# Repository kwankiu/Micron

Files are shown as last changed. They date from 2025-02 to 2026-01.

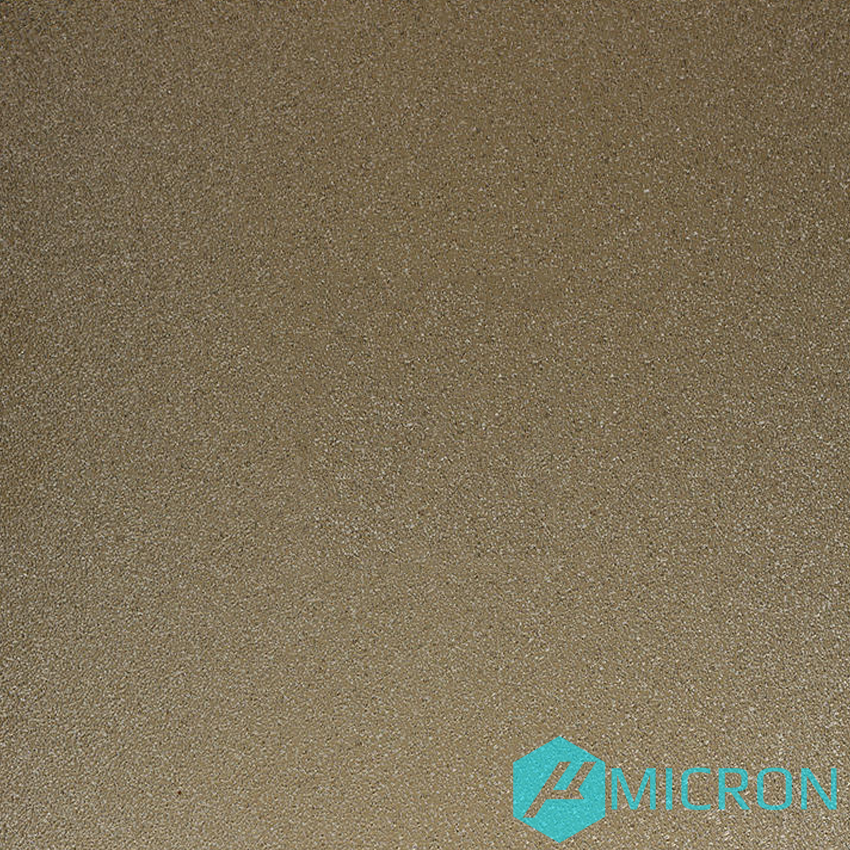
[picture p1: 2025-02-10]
Slicer_Profiles/BedModel/micron_textured.png

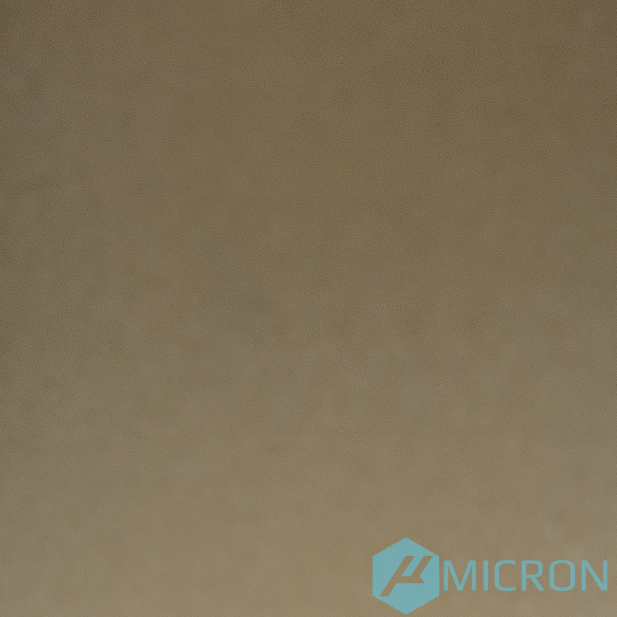
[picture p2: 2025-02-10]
Slicer_Profiles/BedModel/micron_smooth_pei.png

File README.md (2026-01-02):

## Micron M++
Rendering of a Micron build

<p align="center">
  <a aria-label="Stars" href="https://github.com/PrintersForAnts/Micron/stargazers">
    </a> &nbsp;
  <a aria-label="License" href="https://github.com/PrintersForAnts/Micron/blob/master/LICENSE">
    </a> &nbsp;
  <a aria-label="Commits" href="">
    </a> &nbsp;
  <a aria-label="Discord" href="">

</p>

[PFA's Discord](https://discord.gg/doomcube)

[My Micron BOM is here.](https://docs.google.com/spreadsheets/d/1mTU4rc2pGbNT7JGGZr5BcKCps8HXw2-bZYBfcn8UcF8)

### M++ is my own fork of Micron R1 with mods, config and additional STLs

## Changes
- SuperSlicer & OrcaSlicer Profile
- Printer config
- ADXL345 Probe (WIP)
- 230x230 build (WIP)

## Size

<details> 
   <summary>
    120x120 build
    </summary>

## Frame Extrusions
Misumi Part #  |Qty | Notes
 ----|----|----|
HFS3-1515-300 |4 | Blind holes need to be drilled
HFS3-1515-220 |10| Ends need to be tapped (M3)
HFS3-1515-205 |2 |
HFS3-1515-190 |1 |
HFS3-1515-120 |1 |

## Linear Rails
Part  | Qty | Length | Notes
-----|----|----|----|
MGN7H | 6 | 160mm | will work with V0 150mm rails if wanted, but 160mm will work as well and is recommended  
MGN9C OR MGN9H | 1 | 160mm | will work V0 150mm rails but 160 will work as well and is recommended 
</details>

<details>
    <summary>
    180x180 build
    </summary>
    
## Frame Extrusions
Misumi Part #  |Qty | Notes
 ----|----|----|
HFS3-1515-350 |4 | Blind holes need to be drilled
HFS3-1515-280 |10| Ends need to be tapped (M3)
HFS3-1515-265 |2 |
HFS3-1515-250 |1 |
HFS3-1515-180 |1 |

## Linear Rails
Part  | Qty | Length
-----|-----|-----|
MGN7H | 6 | 220mm
MGN9C OR MGN9H | 1 | 220mm 
</details>

<details>
    <summary>
    230x230 build
    </summary>
    
## Frame Extrusions
Misumi Part #  |Qty | Notes
 ----|----|----|
HFS3-1515-400 |4 | Blind holes need to be drilled
HFS3-1515-330 |10| Ends need to be tapped (M3)
HFS3-1515-315 |2 |
HFS3-1515-300 |1 |
HFS3-1515-230 |1 |

## Linear Rails
Part  | Qty | Length
-----|-----|-----|
MGN7H | 6 | 270mm
MGN9C OR MGN9H | 1 | 270mm 
</details>

## No Drop Nuts
There are 2 versions of this mod, 1 from [Zruncho](https://github.com/VoronDesign/VoronUsers/tree/master/printer_mods/zruncho/V0_No_Drop_Nuts) and the other from a user named [Zen3D](https://github.com/VoronDesign/VoronUsers/tree/master/printer_mods/Zen3D/V0_1515_T-nut/). Both of them have their uses. I prefer to use the Zen3D kind just for the fact that the screw can go all the way through the printed part. Zrunchos do have a much nicer fitment into the extrusions but they also dont allow the screw to go all the way through. **NOTE:** the Zruncho nuts will not fit anywhere that has a tab to index to the extrusion - this includes the A/B drives, all idlers, and skirts. If you want to print only one type of nut, use the Zen3d nuts.

## Thank you
Thanks to the following people on Discord who have helped make this printer what it is today. 

- [@KyleGB](https://github.com/Jadecky) - too many additions to name them all
- @TheWarolf#1247
- @L.e.o.p.a.r.d#0990
- @deepfriedheroin#5006
- @JosAr#0517
- @sentein#3903
- @madcat#7838
- @Kyrios#5486
- @faithblinded#1491
- @zruncho#1790
- @Finn#2449
- @clee#1337
- @slidr#4412
- @gfunnymoney#3748
- Jason from LDO
- Voron Dev Team
- all the R1 beta testers
  
[You can support the Micron project on Patreon](https://www.patreon.com/user?u=27661824&fan_landing=true).

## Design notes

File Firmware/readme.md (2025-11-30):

# Micron Firmware Config

run this script in your terminal to download the basic Micron cfg, 

```
cd ~/printer_data/config && curl -s https://api.github.com/repos/PrintersForAnts/Micron/contents/Firmware/printer_data/config | grep download_url | cut -d '"' -f 4 | xargs -n1 curl -sOL
cd ~/printer_data/gcodes && curl -s https://api.github.com/repos/PrintersForAnts/Micron/contents/Firmware/printer_data/gcodes | grep download_url | cut -d '"' -f 4 | xargs -n1 curl -sOL
```

make sure to go through the entire cfg and uncomment the sections required 

* Build Size (120 or 180) 
* MCU
* Toolhead MCU
* Probe

This will download he default config as well as a sample gcode for printing a test cube

to initiate the test cube print, run the macro 

`PRINT_TEST_CUBE` 
then your webui will prompt you to choose which filament type you are using for the test print 


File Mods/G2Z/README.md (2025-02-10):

## Micron Galileo 2 Z-Drive (G2Z)

It is recommened to use the [Z idlers](../R1_Beta/STLs/Z_Idlers/) from the R1 beta folder if using G2Z drives 



The Galileo 2 Z-Drive (G2Z) is designed as a compact Z-drive for the Voron V2 and Micron printers.  It features the same 9:1 planetary gearbox and stepper in an easy-to-assemble package without the need for belts or pulleys (outside of the Z belt and pulley themselves).  This design saves considerable space in the electronics compartment for small V2 printers, as well as the Micron 120 and 180 printers, allowing for more room where it's needed most.

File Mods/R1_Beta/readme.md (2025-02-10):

## Micron R1 Beta 
Rendering of a Micron build
<p align="center">

</p>

<p align="center">
Be sure to check out the Micron R1 beta thread on the Doomcube discord for more information 
</p>

## Change log ##

### 01-20-2025
* fixed issues #143 , #141, #138 , #137
* Updated CAD to RC1 status
* uploaded WIP manual with updated preloaded nut callouts 

### 10-17-2024
* Added G2Z Cad and organized all the STLS (Z drives and skirts) G2Z uses same foot mounts from R1Z and skirt accent pieces 
* fixed Pinned XY joints hole sizes to now all be 3.2mm 
* Updated latest assembly to include [Anthead](https://github.com/PrintersForAnts/AntHead)

### 9-20-2024
* increased tension travel on the front idlers by 5mm (from 3mm to 8mm) , minor changes to the front cover of the idler as well

### 9-18-2024
* fixed incorrect counterbore bridging on the rear bowden entry files (thanks to user named Yell for finding that)

### 9-12-2024
* added CNC gantry top bearing mount
* Updated all the umbilical mounts to accomodate the new top bearing mount, as it was interfearing
* removed the YC8 version of the umbilical
* updated cad assembly to v59 

### 9-10-2024
* Added new top bearing support for a double shear bearing on the AB motors 

### 9-5-2024
* cleaned up main cad assembly 
* posted link to fusion source assembly file to be downloaded
* adjusted gantry files to no longer need built in printed shim, now there are shims on both sides of every bearing stack 

### 9-3-2024
* added missing filter files 
* fixed naming issues on certain files 

### 9-2-2024
* added new under bed carbon filter
* started on CAD assembly clean up 
* renamed various files 

### 8-22-2024 
* cleaned up files

### 8-11-2024
* updated the Hula foot mounts to the latest version that works with the bottom panel
* added new TFT35 display front skirt 
* updated latest cad assembly v55
* removed old cad files no longer needed (moved hula cad files into main assembly)

### 8-2-2024
* organized panel clip files
* updated latest cad assembly v54
* added dual color rear bowden entry option

### 8-1-2024
* Updated Z drives for better printability to match new skirt accent pieces
* Added under bed filter from KyleGB to the main repo (still need STLs)

### 7-27-2024
* fixed waveshare accent pieces
* updated latest cad assembly v52
* updated skirts with new accent pieces as well as bottom panel mounting provisions

### 7-25-2024
* Updated z belt cover accent cover to fit better
* added twist lock panel clips for 3mm foam and panels
* fixed printing orientation for rail stops and umbilical mounts

### 7-23-2024
* Updated R1 Skirts to now include accent strips along the bottom as well as allow for a bottom panel to fit
* Updated skirts to they are all the same height , some had about ~1mm difference between them 
* Updated the waveshare mount to now us m2 self tapping screws instead of filament to keep bezel on 
* Updated Z drive foot mount to accommodate  bottom panel 

### 7-23-2024
* Update Beacon mount to work with older Rev D beacon probes 
* Added a new rear bowden entry set, supporting m10 collet, ECAS collet, or No collet 
* Added R1 style stock panel clips (tool less panel clips are coming soon as an option as well)
* Added fixed Z belt covers to better fit with the R1 Z belt location
* Organized the panel file directory 

### 7-15-2024
* Added Beacon probe mount

### 7-08-24
* Added 120x120 build R1 Cad assembly
* Added rear skirts for 120x120 builds 
* Organized files into 120 and 180 specific folders 

### 7-05-24
* added rear power inlet skirts
* updated printed rail stops to match the style of R1 update (low poly look)
* added keystone blank model to fill the keystone slots on the rear skirt if not used 

### 7-02-24
* updated Z drive tensioner body to use longer m3x25 instead of m3x20
* added optional Hula feet adapters for R1 and G2Z
* updated latest cad assembly

### 6-18-24
* uploaded side skirts and 4.3 waveshare display front skirt

### 6-2-24
* changed hex pattern on Z drives to make them easier to print 

### 5-21-24
* adjust the location of the Z gantry belts pulley to fit in the front idlers better ([#124](https://github.com/PrintersForAnts/Micron/issues/124))

### 5-14-24
* fixed z drive issue with inconsistencies with both A and B z drives ([#120](https://github.com/PrintersForAnts/Micron/issues/120))
* updated z tensioner bearing overhang to be easier to print ([#122](https://github.com/PrintersForAnts/Micron/issues/122))

### 5-7-24
* Added ziptie spot on to klicky dock

### 5-6-24
 * Updated Z drives to fit powge and formbot metal 64T pulleys ([#115](https://github.com/PrintersForAnts/Micron/issues/115))
 * Updated Z idlers to fit toothed pulleys with a flange of 13mm OD ([#116](https://github.com/PrintersForAnts/Micron/issues/116))
 * raised klicky dock , it was hanging too low ([#117](https://github.com/PrintersForAnts/Micron/issues/117))
 * updated spool holder to now work with 3mm foam ([#118](https://github.com/PrintersForAnts/Micron/issues/118))

### 4-6-24
 * added pushed rigid z joints
 * new z belt covers
 * new bowden tube holder
 * new removable spool holder (modified from LDOs)

### 4-5-24
  *  Added Nema14 Z motor mounts

### 4-3-24
  * New beta rev2 Z drives with the 152mm belt loops
  * Shrunk entire body by 5mm or so
  * rotated the Z drives 180deg, this makes it easier to retention the closed loop belts after they are assembled if needed (thanks [@Squirrel-brain](https://github.com/Squirrel-brain)) 

### Initial Beta Release
Gantry 
  * Swapped rear extrusion and Z chain around
  * Fixed all belt path issues with the gantry
  * Gave every piece a low poly / stealthy look to them
  * New z joints that are stronger/ less prone to cracking
  * Added support for 3mm pins OR screws for the gantry
  * Removed support for the printed Z chain (will revisit later)
  * Implemented the BFI idlers for the AB belts
  * Modified the BFI idlers from clees repo to fix the belt path for the R1 gantry 
    
Z axis
  * New Z drives that use 152mm belt loops with proper belt tensioning 
  * Implemented the BZI idlers for the Z belts
  * Modified BZI to support both toothed idlers and bearing stacks (there are different parts named accordingly)

Panels/Door/Skirts
  * New door hinge/ latch system that no longer needs the magnet latch on the inside of the printer
  * Door now needs 3mm foam to help seal the enclosure better
  * Panel clips will be coming later as will skirts

## BOM Changes (Subject to change)
Item  |Qty | Notes
 ----|----|----|
GT2-16-Toothed Idler | 6 | XY-Joints and Z idlers now use toothed idlers by default, bearing stacks will still work 
GT2-152mm closed loop belt | 4 | New Z drives use 152mm belt loops instead of the 188mm 
screws | IDK | i havent gone through and checked the changes for the hardware as of yet 
MGN9H | 1 | X rail is now going to be spec as an MGN9H rail instead of MGN9C to support boop natively 
Klicky_PCB | 1 | now offical support optional as standard klikcy is still supported 
BIQU_microprobe | 1 | also now an official supported mount for those that want to use it

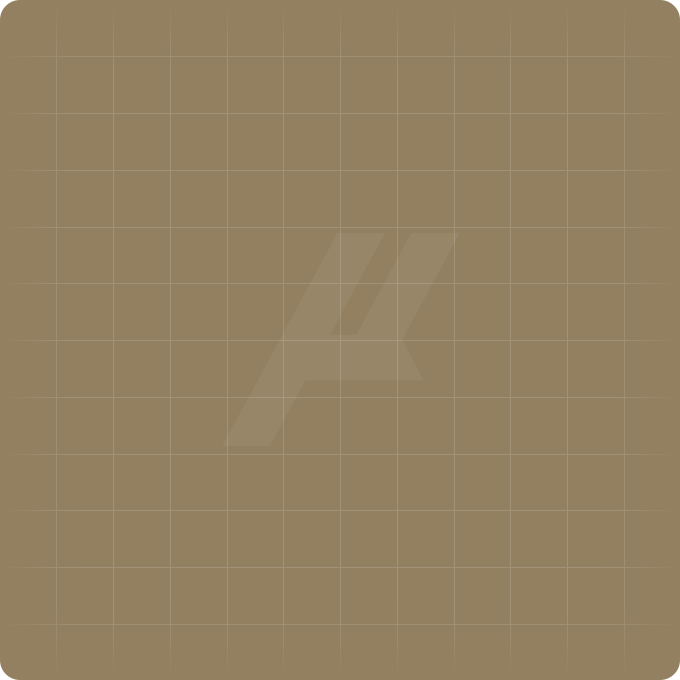
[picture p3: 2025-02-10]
Slicer_Profiles/BedModel/micron-120-grid.png

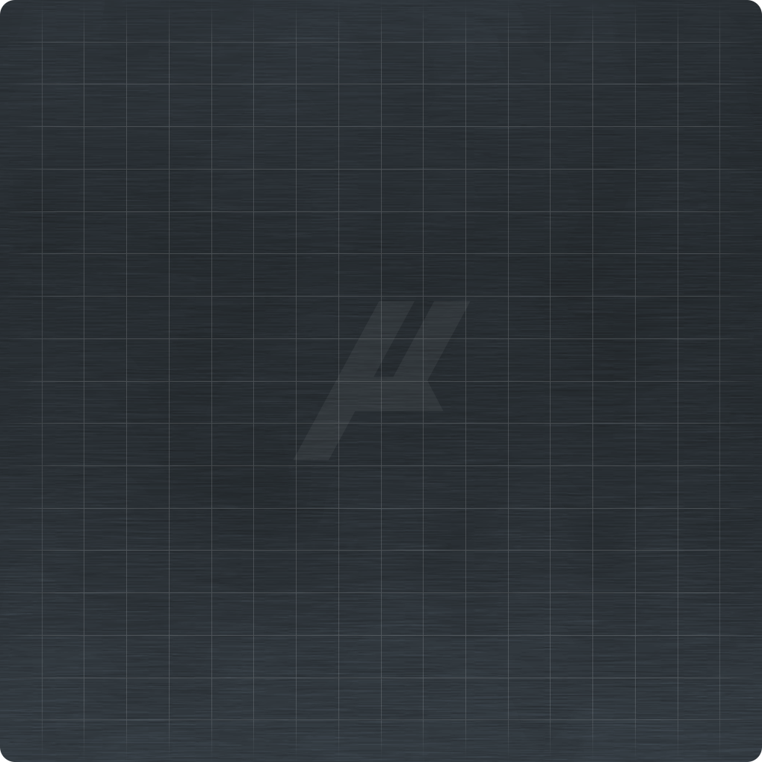
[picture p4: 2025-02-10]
Slicer_Profiles/BedModel/micron-180-grid-blue.png

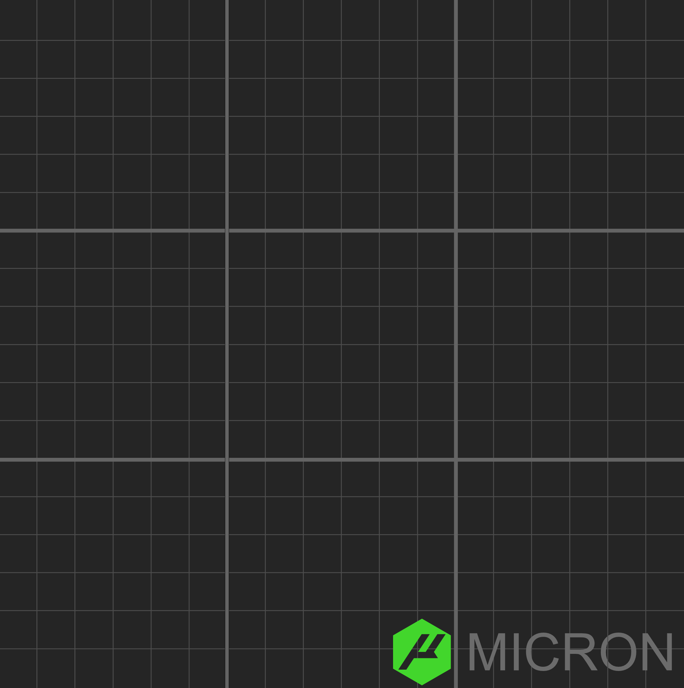
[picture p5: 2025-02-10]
Slicer_Profiles/BedModel/micron-180-grid-green.png

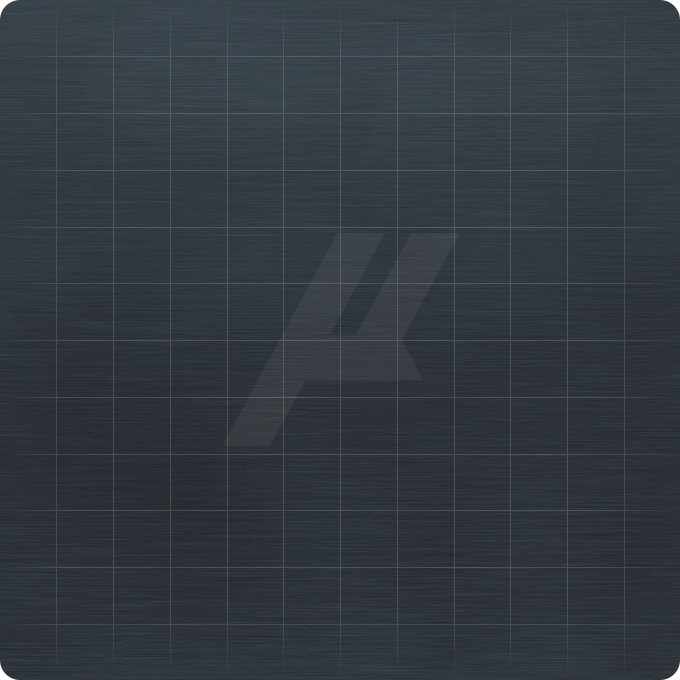
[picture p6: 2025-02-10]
Slicer_Profiles/BedModel/micron-120-grid-blue.png

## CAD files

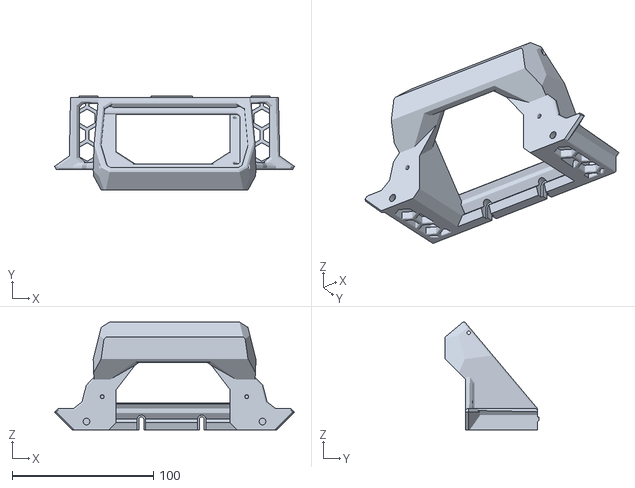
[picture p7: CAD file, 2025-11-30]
STLs/Skirts/Displays/TFT35/main_housing.stl
169.9 x 66.6 x 76.4

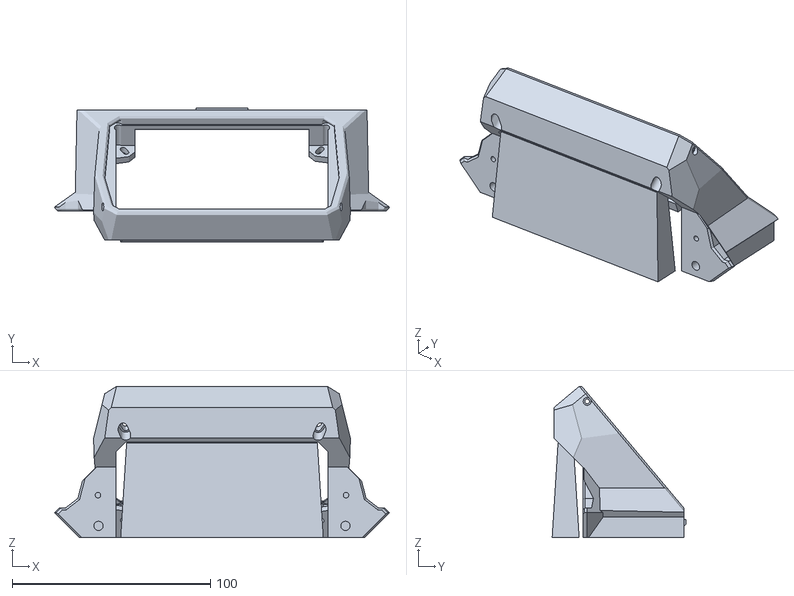
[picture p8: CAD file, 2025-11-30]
STLs/Skirts/Displays/Waveshare43_BTT43/waveshare_btt43_main_housing_x1.stl
169.0 x 67.5 x 76.4

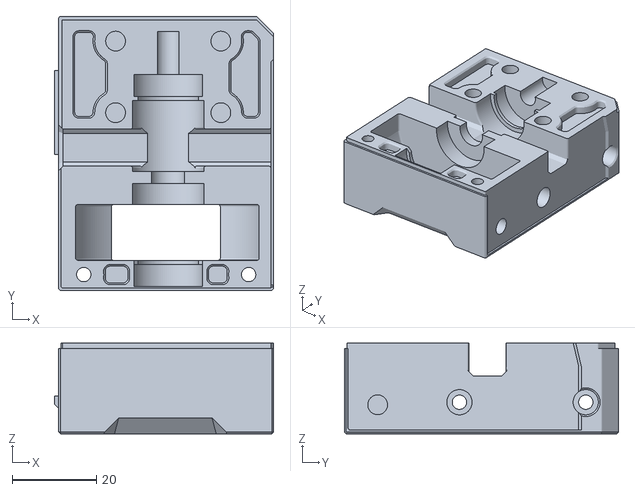
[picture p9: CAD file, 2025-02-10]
STLs/Z_Drive/main_body_a_x2.stl
52.0 x 65.1 x 21.5

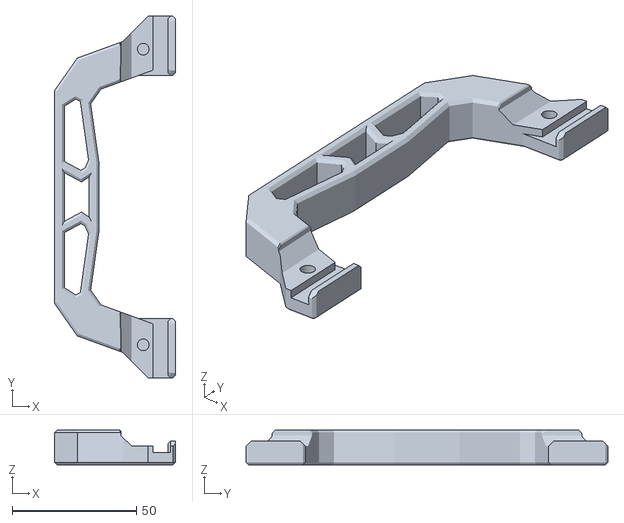
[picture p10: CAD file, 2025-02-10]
STLs/MISC/main_handle_x2.stl
48.8 x 145.7 x 14.1

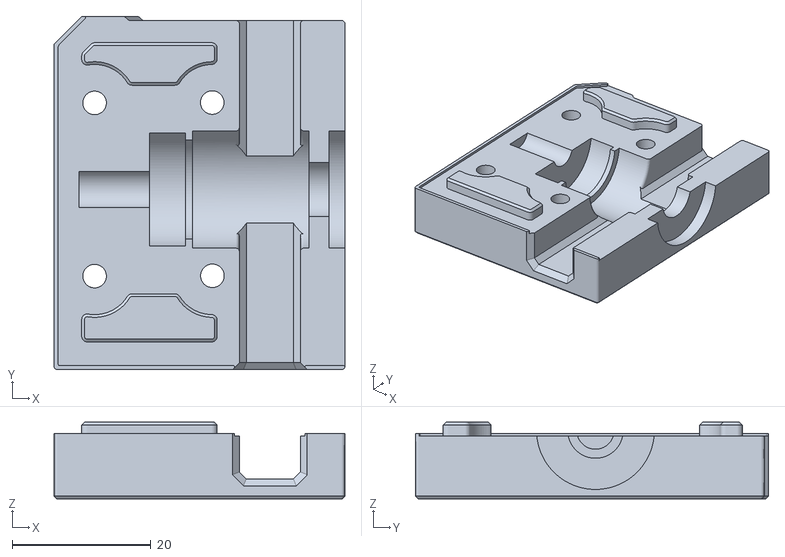
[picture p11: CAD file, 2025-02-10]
STLs/Z_Drive/[a]_shaft_assembly_cover_b_x2.stl
42.0 x 51.0 x 11.0

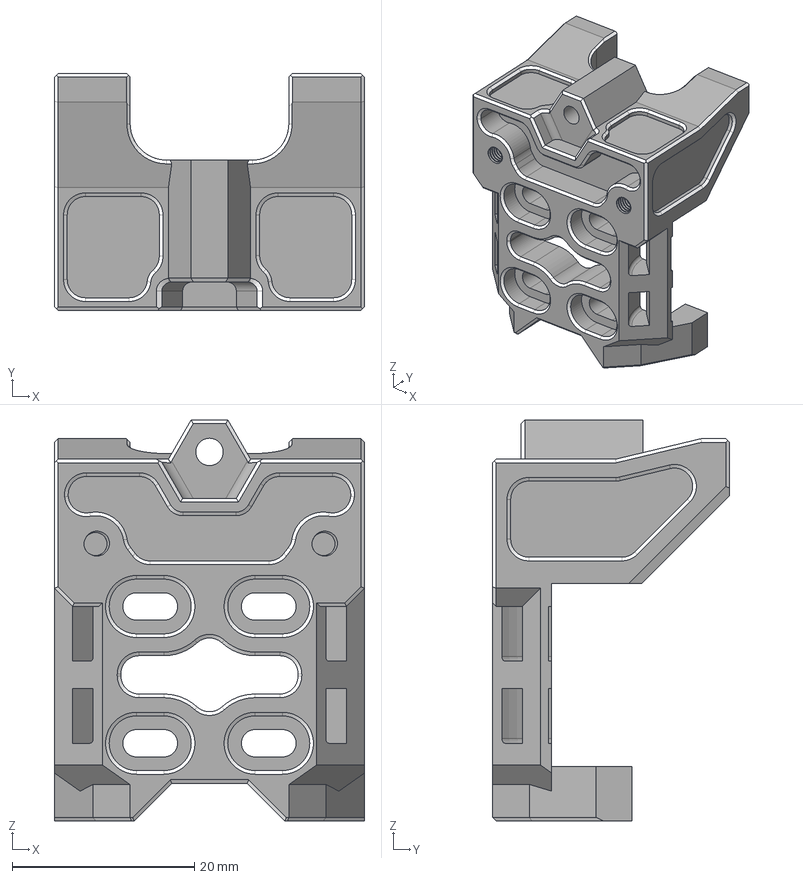
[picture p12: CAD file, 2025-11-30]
CAD/SubAssemblies/CNC_Carriage.step
34.0 x 26.0 x 44.0 mm
MiniSB X Carriage
MGN9H v1 v1
MiniSB X Carriage (2)
M3x6 SCHS (1)
M3x6 SCHS (1) (1)

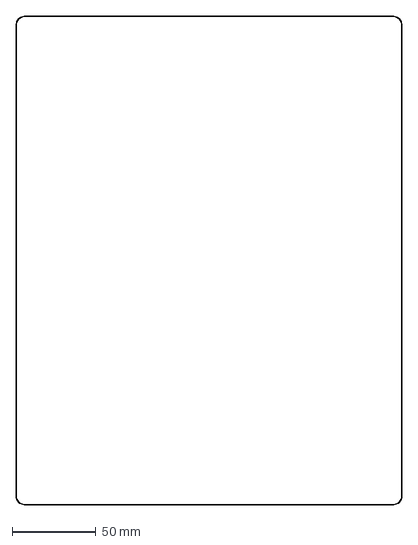
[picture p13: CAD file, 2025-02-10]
Drawing_DXFs/120/door_panel_x1.dxf
230.0 x 291.0 mm

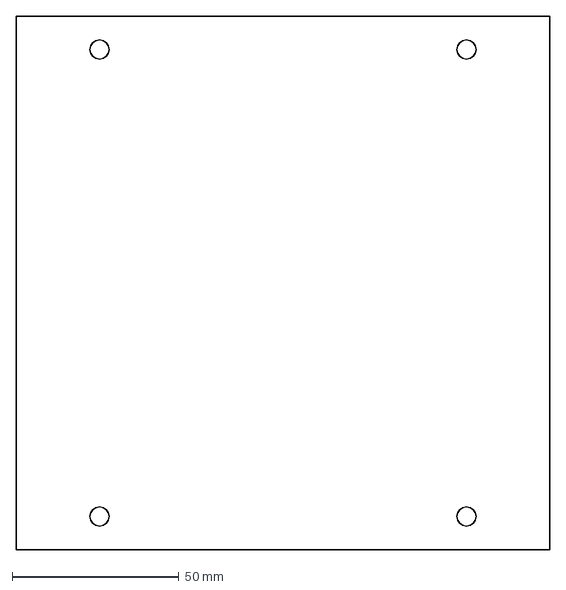
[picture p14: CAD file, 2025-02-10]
Drawing_DXFs/180/Micron-160-Bed.dxf
160.0 x 160.0 mm

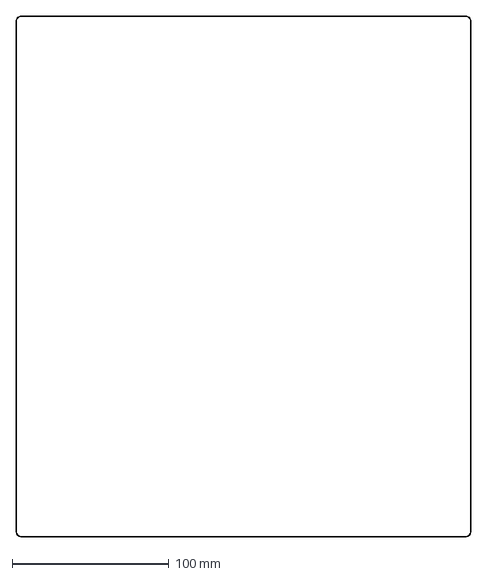
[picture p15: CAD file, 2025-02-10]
DXFs/TRANSPARENT_Side_and_DoorPanel_x3.dxf
290.0 x 332.0 mm

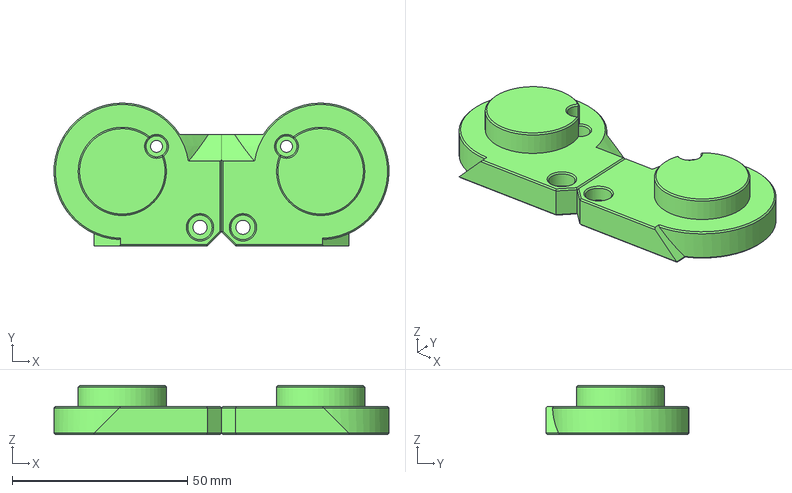
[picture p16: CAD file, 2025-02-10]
Mods/G2Z/CAD/Micron_Hula_G2Z_Feet.step
95.6 x 40.8 x 14.0 mm
Micron_Hula_G2_Z_Drive_Base_Plate_A
Micron_Hula_G2_Z_Drive_Base_Plate_B

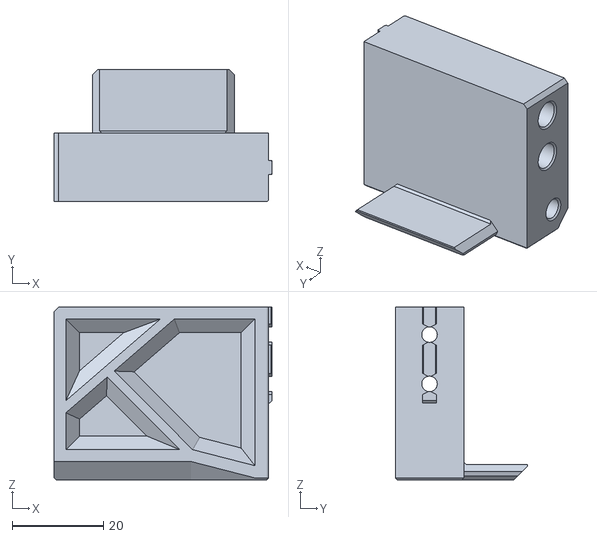
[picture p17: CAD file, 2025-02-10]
Mods/G2Z/STLs/Z_Drives/g2_z_skirt_corner_b_x2.stl
47.7 x 29.0 x 37.8

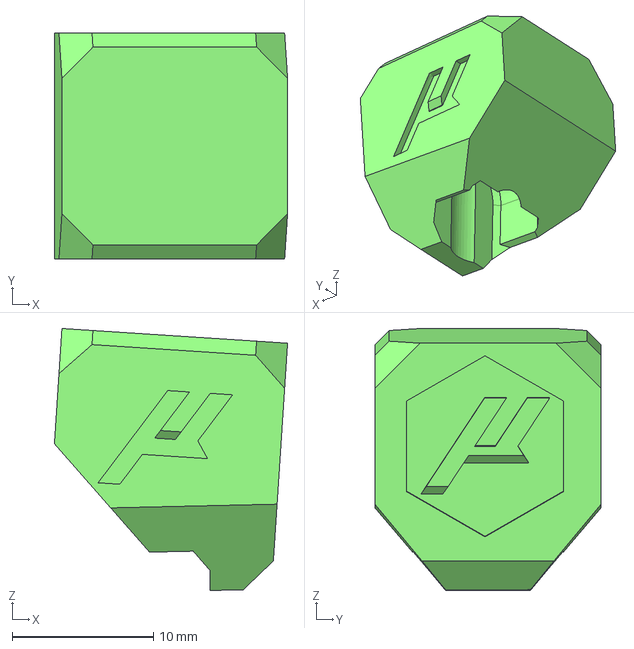
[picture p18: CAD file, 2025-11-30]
Mods/hartk1213/Dummy13_Parts/Micron_Cube_head.step
16.5 x 16.0 x 18.5 mm

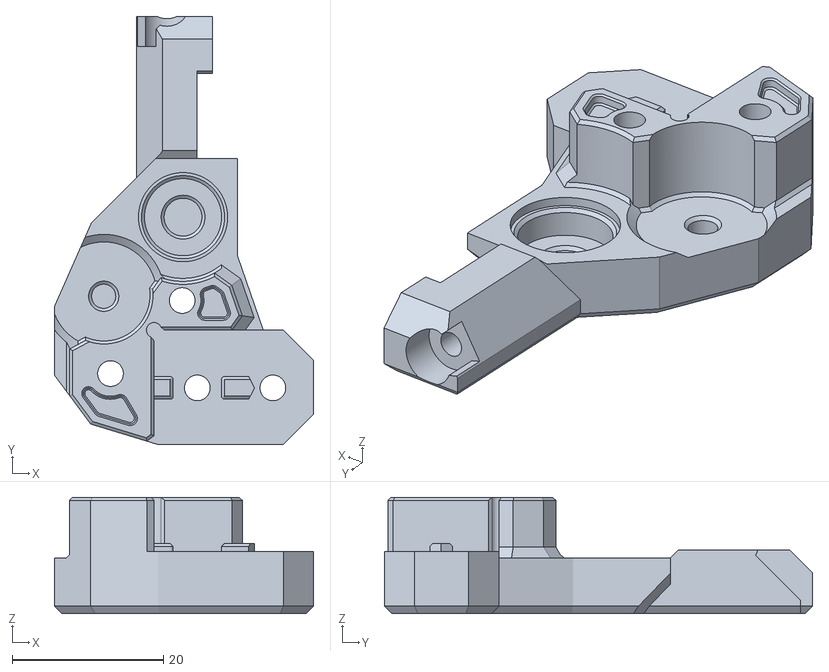
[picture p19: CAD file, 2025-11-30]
Mods/hartk1213/LiveIdler_XY_Joints_LeafCutter/xy_joint_upper_left_live_idlers_LC_x1.stl
34.3 x 56.7 x 15.4

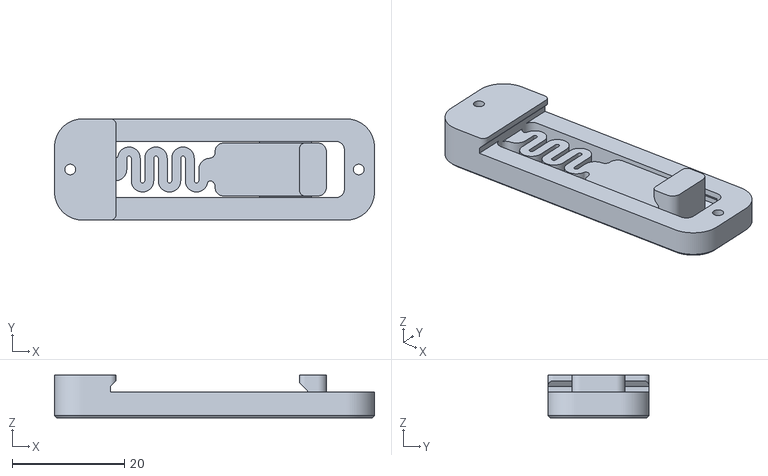
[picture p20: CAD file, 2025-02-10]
Mods/R1_Beta/STLs/Electronics/pcb_din_clip_x3.stl
56.9 x 18.0 x 7.60

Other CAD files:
STLs/Z_Drive/[a]_shaft_assembly_cover_a_x2.stl
STLs/Z_Drive/main_body_b_x2.stl
Mods/R1_Beta/STLs/MISC/Filter/[a]_cartridge_removal_key.stl
Mods/R1_Beta/STLs/Panels/corner_clip_x16.stl
CAD/SubAssemblies/1515_ParametricPanelClips.f3z
DXFs/180_bottom_panel.dxf
DXFs/BLACK_DeckPanel_x1.dxf
DXFs/BLACK_RearPanel_x1.dxf
DXFs/Micron+_MIC6_Bed.step
DXFs/Micron-PrusaMini-Mic6-Bed.dxf
DXFs/TRANSPARENT_TopPanel_x1.dxf
Drawing_DXFs/120/back_panel_x1.dxf
Drawing_DXFs/120/bottom_panel_x1.dxf
Drawing_DXFs/120/deck_panel_x1.dxf
Drawing_DXFs/120/micron_backers.dxf
Drawing_DXFs/120/side_panel_x2.dxf
Drawing_DXFs/120/top_panel_x1.dxf
Drawing_DXFs/180/BottomPanel.dxf
Drawing_DXFs/180/Micron_PrusaMini_MIC6_Bed.step
Mods/G2Z/STLs/Skirts/side_skirt_a_x2.stl
Mods/G2Z/STLs/Skirts/side_skirt_b_x2.stl
Mods/G2Z/STLs/Z_Drives/[a]_g2_z_drive_base_plate_a_x2.stl
Mods/G2Z/STLs/Z_Drives/[a]_g2_z_drive_base_plate_b_x2.stl
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

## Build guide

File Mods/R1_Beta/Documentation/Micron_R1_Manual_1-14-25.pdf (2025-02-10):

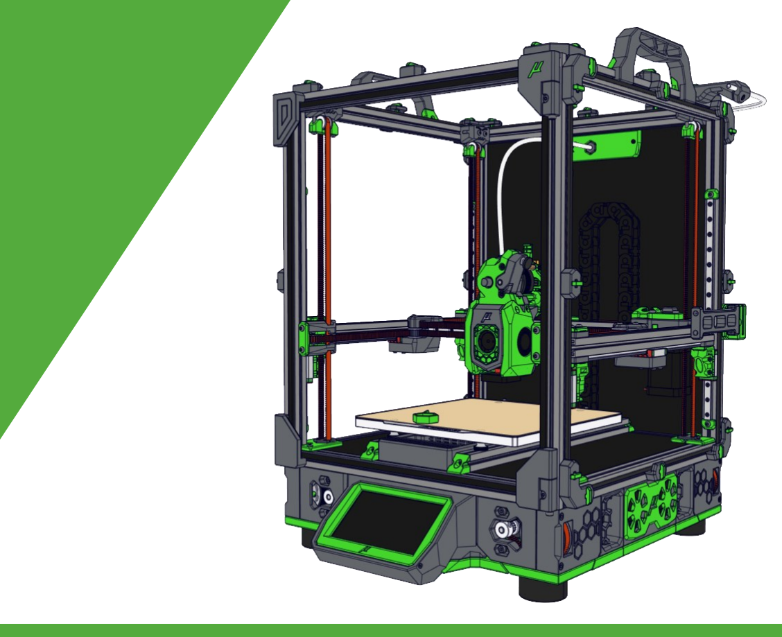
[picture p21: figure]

## VERSION 01/14/2025

# ASSEMBLY MANUAL

Everything is smaller but the price.

M

R1

# icron

TABLE OF CONTENTS

INTRODUCTION | MICRON

## STL FILE KEY

## PRINT GUIDELINES

The STL naming convention used for Micron is the same as that used for VORON printers:

The recommended print settings are also those used for VORON printers:

### PRIMARY COLOR

Example
z_drive_main_a_x2.stl
These files will have nothing at the start of the filename.

### ACCENT COLOR

Example
[a]_z_drive_baseplate_a_x2.stl These files will have ‘’[a]’’ to the front to mention that they are intended to be printed with an accent color.

### QUANTITY REQUIRED

Example
[a]_z_drive_baseplate_a_x2.stl If a file ends with ‘’_x#’’, that is telling you the quantity of that part required to build this system..

FDM MATERIAL
Micron was designed for ABS. Use other plastics at your own discretion.
LAYER HEIGHT
Recommended : 0.2mm
EXTRUSION WIDTH
Recommended : Forced 0.4mm INFILL PERCENTAGE
Recommended : 40%

INFILL TYPE
Grid, Gyroid, Honeycomb, Triangle, Cubic, Adaptive Cubic.
WALL COUNT
Recommended : 4
SOLID TOP/BOTTOM LAYERS
Recommended : 5
SUPPORTS REQUIRED
If the part needs supports, they are built into the model.
INTRODUCTION | MICRON

HOW TO GET HELP

If you need assistance with your build you can head over the DOOMCUBE Discord server and post your questions ( typically in the #micron_build_questions channel ). It is the primary help channel for the Micron! You can also check the Github page for the latest releases.

DISCO? OH …DISCORD
If you need assistance with your build you can head over the DOOMCUBE Discord server and post your questions ( typically in the #micron_build_questions channel ). It is the primary help channel for the Micron!

GIT GUD
If you want to stay up to date on the latest files for Micron. The github page is the only source for the latest files.
HARDWARE - REFERENCES | MICRON

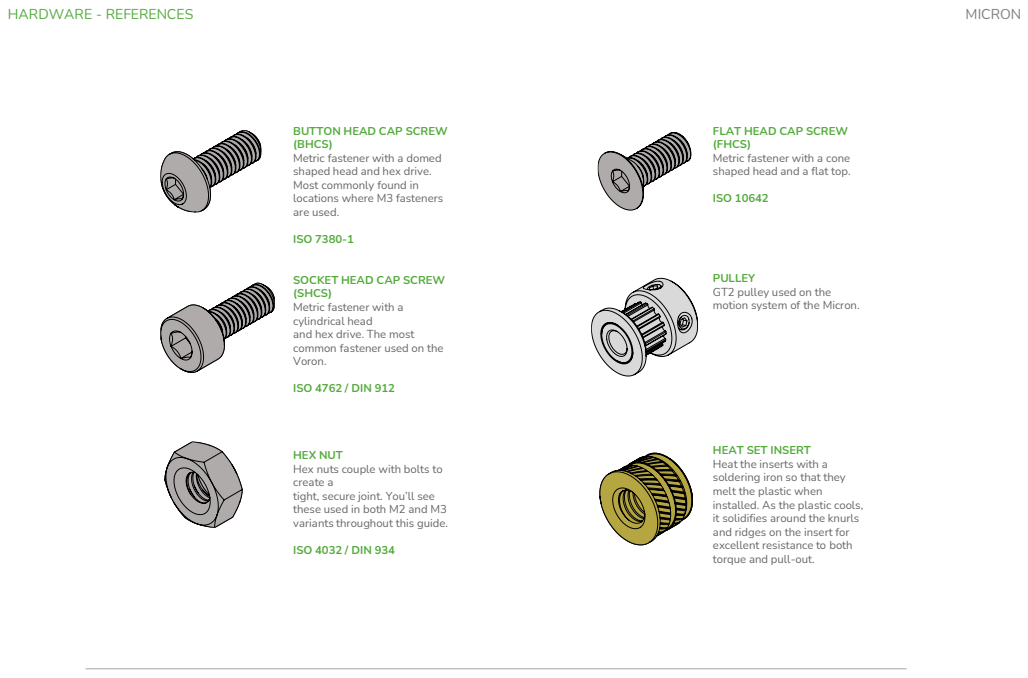
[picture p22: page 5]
HARDWARE - REFERENCES; MICRON

BUTTON HEAD CAP SCREW
(BHCS)
Metric fastener with a domed
shaped head and hex drive.
Most commonly found in
locations where M3 fasteners
are used.
ISO 7380-1

FLAT HEAD CAP SCREW
(FHCS)
Metric fastener with a cone
shaped head and a flat top.
ISO 10642

SOCKET HEAD CAP SCREW
(SHCS)
Metric fastener with a
cylindrical head
and hex drive. The most
common fastener used on the
Voron.
ISO 4762 / DIN 912

PULLEY
GT2 pulley used on the
motion system of the Micron.

HEAT SET INSERT
Heat the inserts with a
soldering iron so that they
melt the plastic when
installed. As the plastic cools,
it solidifies around the knurls
and ridges on the insert for
excellent resistance to both
torque and pull-out.

HEX NUT
Hex nuts couple with bolts to
create a
tight, secure joint. You’ll see
these used in both M2 and M3
variants throughout this guide.
ISO 4032 / DIN 934

SELF TAPPING SCREW
Fastener with a pronounced
thread profile that is screwed
directly into plastic.

F623 BEARING
A ball bearing with a flange
used in various gantry
locations.

M3 SHIMS
Not to be confused with
stamped washers. These are
used in all M3 call-out
locations in this manual.
3x6x0.5 DIN 988

625 BEARING
A ball bearing with used in
the Z drive.

5mm x 47mm Shaft
Steel shaft, 5mm in diameter,
47mm long with a flat ground
on it used in the Z drive gear
box assembly

GRUB SCREW (GS)
Metric Socket Cup Point Set
Screws (also called Hollow
Point Grub Screws) are fitted
with a concave cup point,
which allows them to fit
closely against a rounded
surface such as a motor shaft.
ISO 4029/ DIN 916

MICRON Logo
Look for Micron Logo next to the printed part, this is a direct link to the file on the github repo.

ATTENTION BUBBLE
This logo denotes steps that are common areas that
mistakes can occur.

HARDWARE - REFERENCES

M3x8 SHCS

Look for the GREEN call
outs to mention the
various hardware used
(5) Bottom – 180

Look for the BLACK call outs to mention the preloaded M3 nuts, NOTE: some of them are specific to the size of printer and will be in bold at the end

MICRON

(3) outside

Look for the GRAY call outs to mention the preloaded M3 nuts that are optional, Some of the printed parts have a printed twist lock version to attach to the frame OR a screwed-on version. If you choose to use the twist lock then you can ignore the gray nut call outs

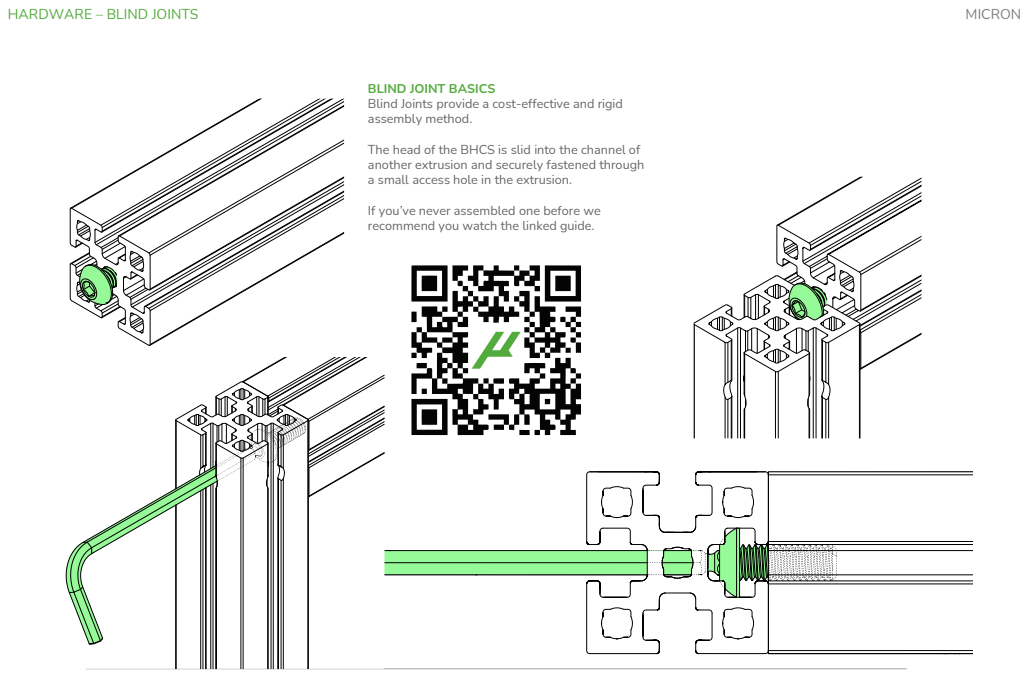
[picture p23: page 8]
HARDWARE – BLIND JOINTS; MICRON

BLIND JOINT BASICS
Blind Joints provide a cost-effective and rigid
assembly method.
The head of the BHCS is slid into the channel of
another extrusion and securely fastened through
a small access hole in the extrusion.
If you’ve never assembled one before we
recommend you watch the linked guide.

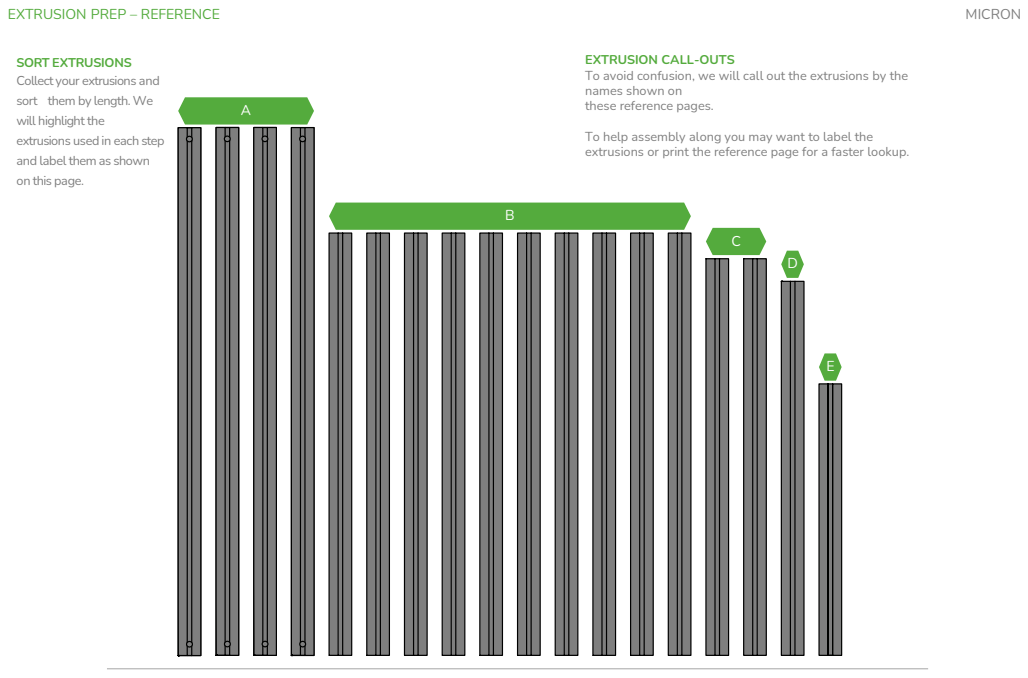
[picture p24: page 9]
EXTRUSION PREP – REFERENCE; MICRON

SORT EXTRUSIONS
Collect your extrusions and
sort them by length.We
will highlight the
extrusions used in each step
and label them as shown
on this page.

EXTRUSION CALL-OUTS
To avoid confusion, we will call out the extrusions by the
names shown on
these reference pages.
To help assembly along you may want to label the
extrusions or print the reference page for a faster lookup.

BED EXTRUSIONS?
Some frame kits come with bed
extrusions that are mounted using
blind joints. These will end up being 2
longer extrusions and 8 B extrusions.

MULTIPLE VIEWS
The views shown are the left, front, right, and
bottom views of each extrusion.

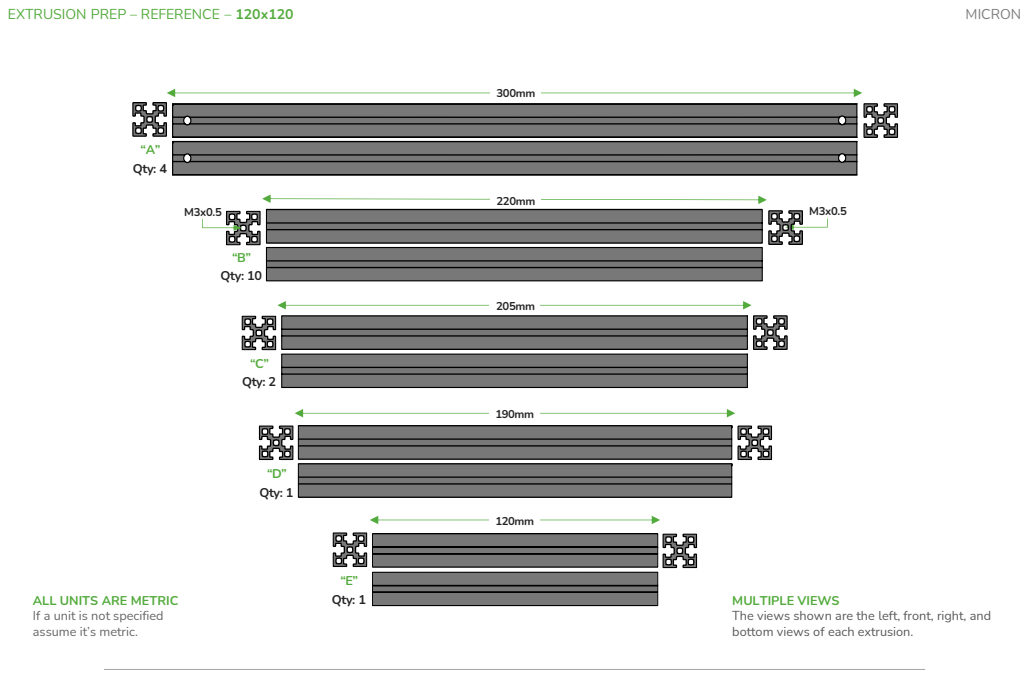
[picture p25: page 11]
“A” Qty: 4; “B” Qty: 10; “C” Qty: 2; “D” Qty: 1; “E” Qty: 1; MICRON

EXTRUSION PREP – REFERENCE – 120x120

ALL UNITS ARE METRIC
If a unit is not specified
assume it’s metric.

MULTIPLE VIEWS
The views shown are the left, front, right, and
bottom views of each extrusion.

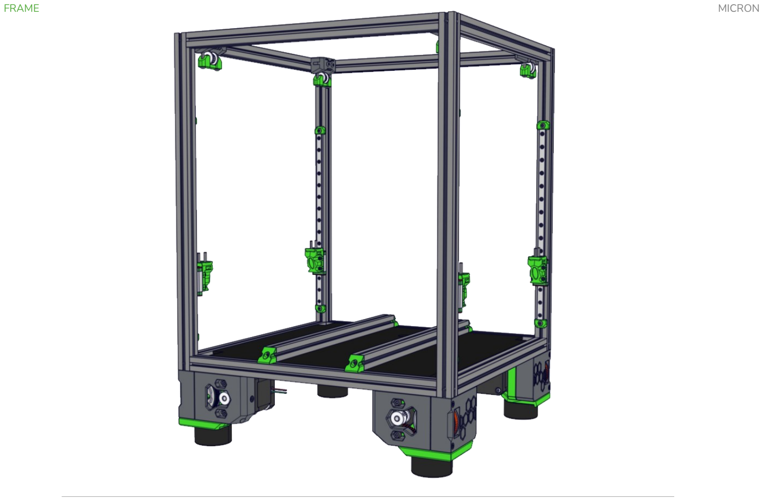
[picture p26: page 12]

FRAME | MICRON

PREPARE 8 EXTRUSIONS
These extrusions are going to be used in
this section. Prepare them as shown above
by partially threading in an M3x8 BHCS
in either side.

POPULATING NUT CARRIERS
Pictured shows all the m2 nuts populated, but depending on how much M2 hardware you sourced, you may not be able to fully populate the M2 Nut Adapters if that happens, skipping

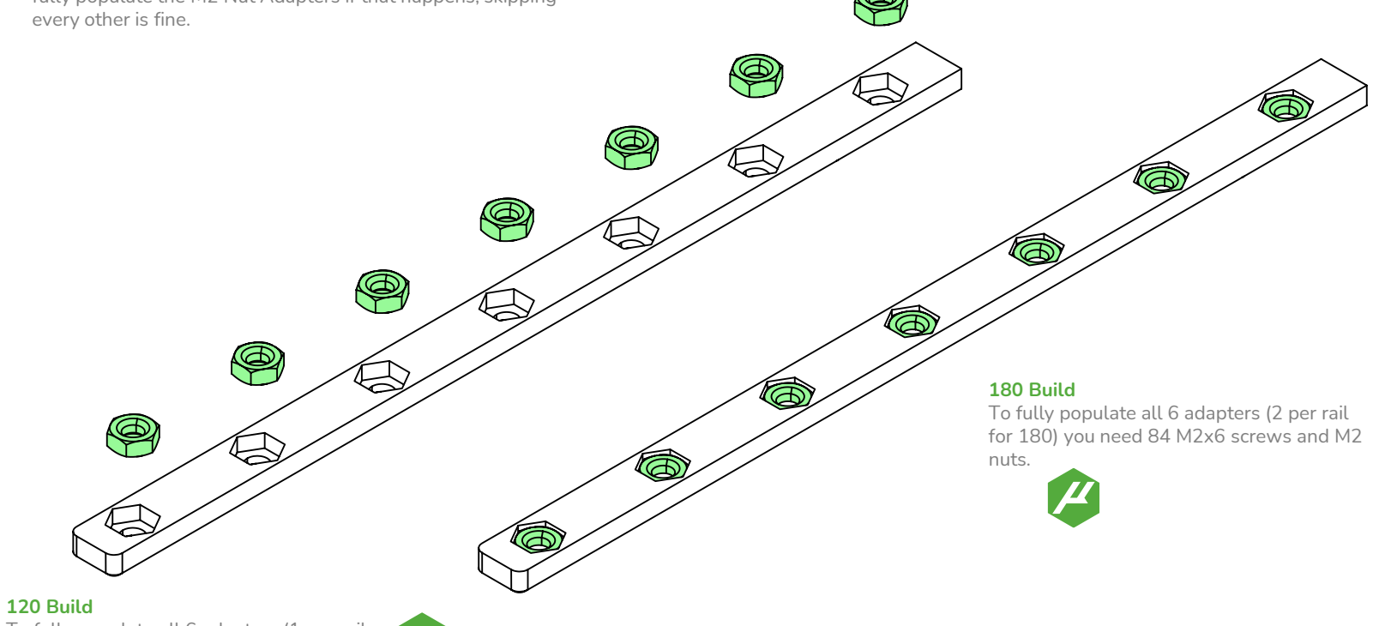
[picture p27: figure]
every other is fine.; 180 Build; for 180) you need 84 M2x6 screws and M2 nuts.; 120 Build

To fully populate all 6 adapters (2 per rail

To fully populate all 6 adapters (1 per rail for 120) you need 60 M2x6 screws and M2 nuts.

FRAME – Z RAILS | MICRON

M2x6 SHCS

M2 Hex Nut

Z RAILS ALIGNMENT

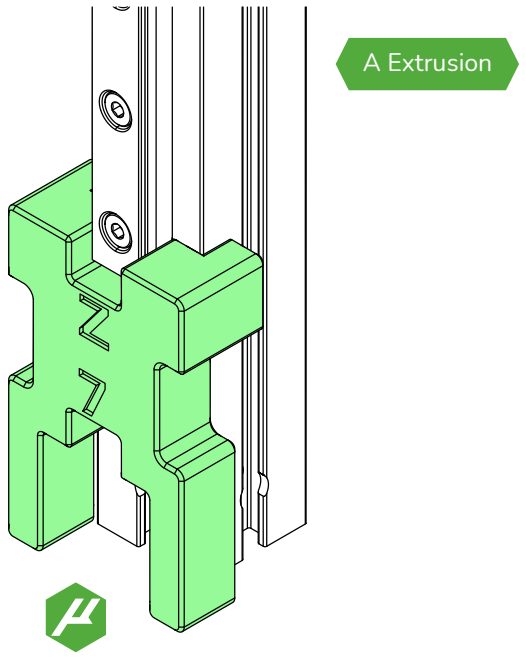
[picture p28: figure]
A Extrusion

Z rails are mounted before assembly of the frame. Stand up one of the A extrusions and use the printed rail alignment tool as shown to align the bottom of the rail. The rail end should be 36mm from the bottom of the extrusion. Use a second rail alignment tool on the upper half of the rail, using the section marked ‘7’, to properly center the rail on the extrusion. Tighten the screws, being careful to maintain the alignment provided by the printed tools. Repeat this process for all 4 A extrusions and their rails.

FRAME – Z RAILS | MICRON

RAIL STOPS
With the Z rails installed, the rail stops can now be added to both ends. Loosely screw an M3x8 BHCS. Repeat for both ends of all 4 Z rails. Now you can work on the build without risking a Z carriage flying off its rail.

WHERE’S THE NUT!?
The instructions won’t call out nuts that were inserted in a previous step, nor nuts that can be easily inserted in the current step. if a screw does NOT thread into a nut we will explicitly state this. You can assume that all screws that enter extrusion slots thread into a nut.
FRAME – Z RAILS | MICRON

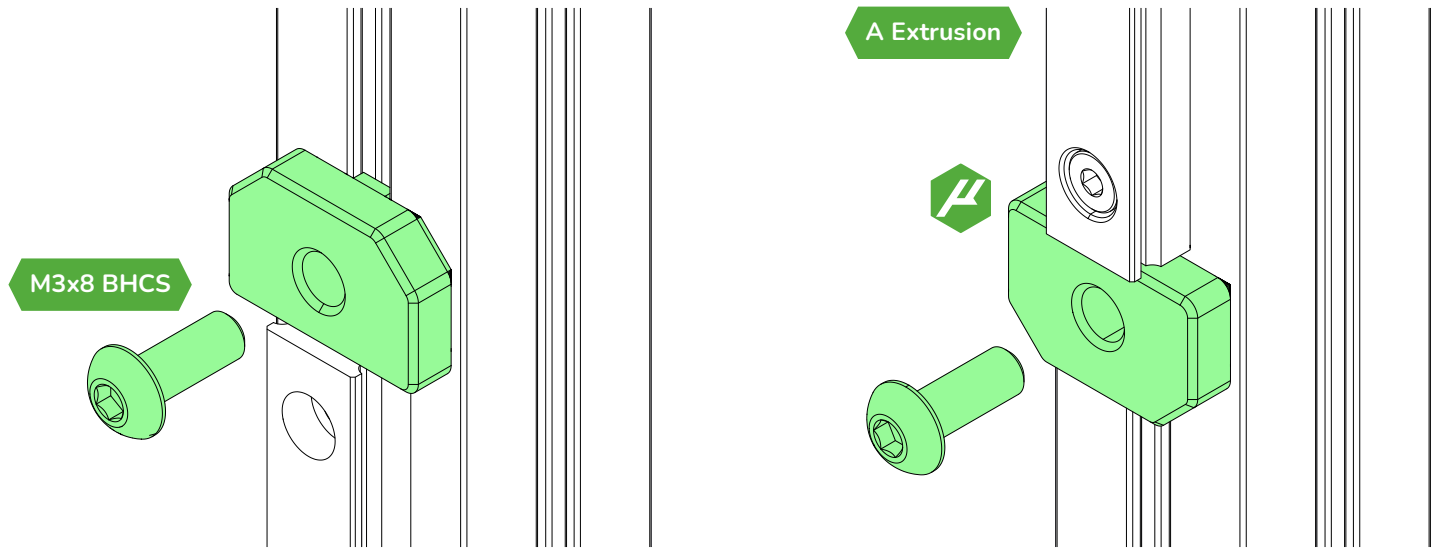
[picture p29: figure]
M3x8 BHCS; A Extrusion
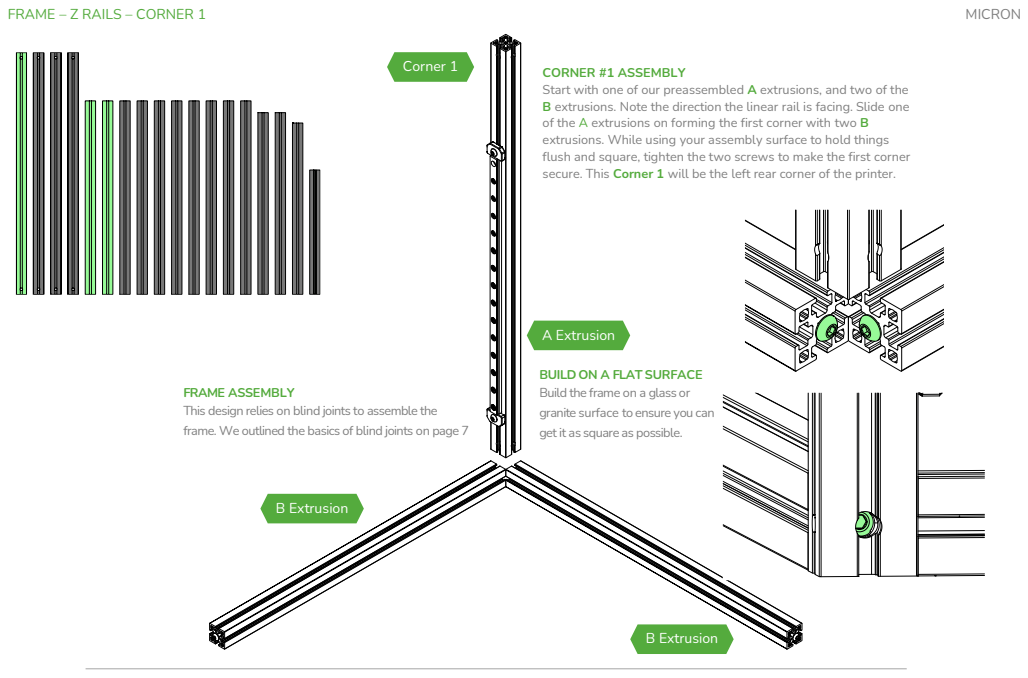
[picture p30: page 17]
B Extrusion; A Extrusion; Corner 1; MICRON

FRAME – Z RAILS – CORNER 1

CORNER #1 ASSEMBLY
Start with one of our preassembled A extrusions, and two of the
B extrusions. Note the direction the linear rail is facing. Slide one
of the A extrusions on forming the first corner with two B
extrusions. While using your assembly surface to hold things
flush and square, tighten the two screws to make the first corner
secure. This Corner 1 will be the left rear corner of the printer.

BUILD ON A FLAT SURFACE
Build the frame on a glass or
granite surface to ensure you can
getit as square as possible.

FRAME ASSEMBLY
This design relies on blind joints to assemble the
frame. We outlined the basics of blind joints on page 7

FRAME – Z RAILS – CORNER 2

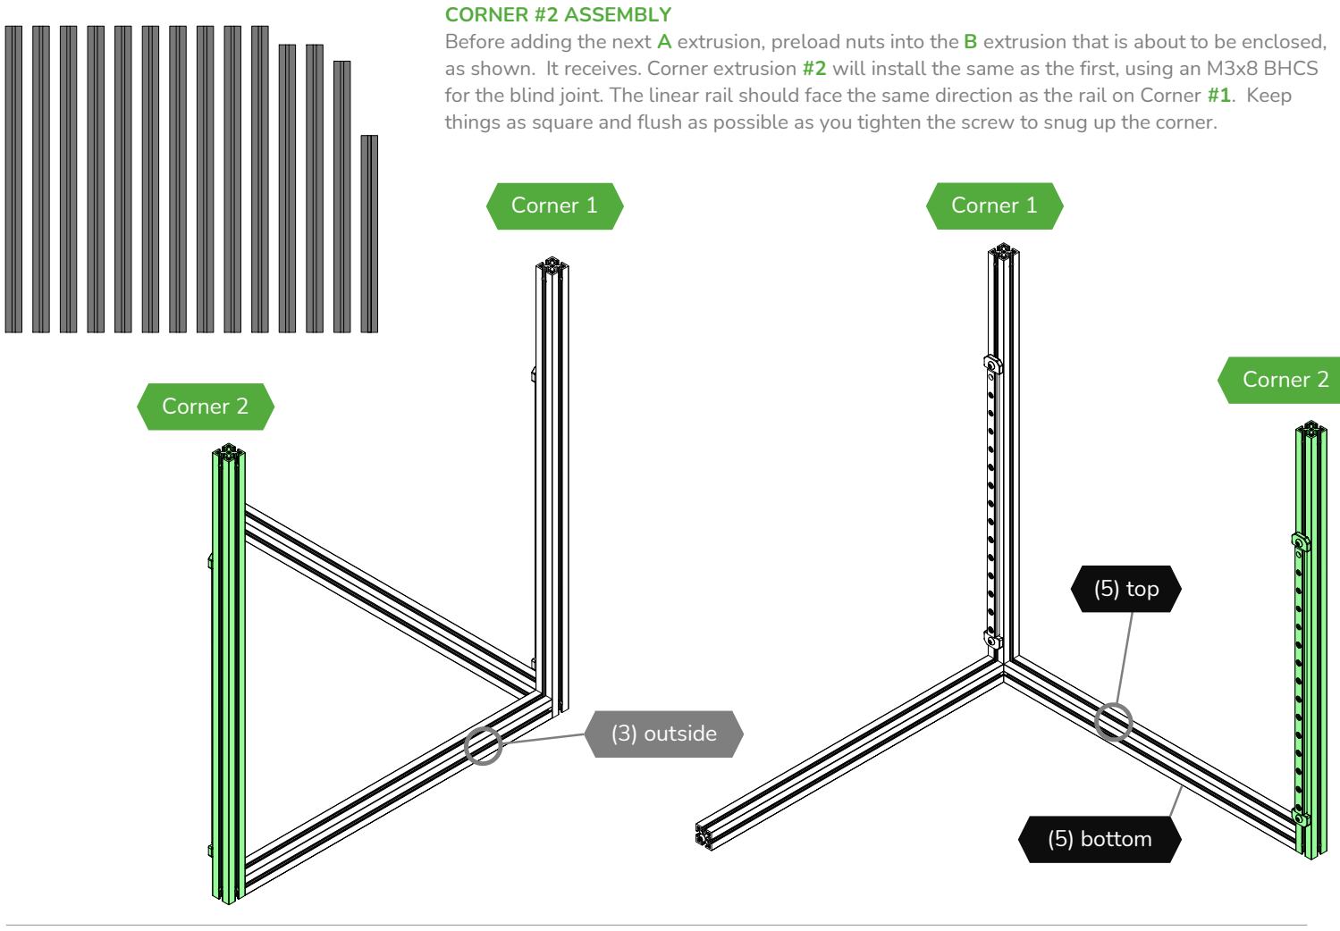
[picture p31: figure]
(5) top; (3) outside; (5) bottom; CORNER #2 ASSEMBLY; Corner 2; Corner 1

Before adding the next A extrusion, preload nuts into the B extrusion that is about to be enclosed, as shown. It receives. Corner extrusion #2 will install the same as the first, using an M3x8 BHCS for the blind joint. The linear rail should face the same direction as the rail on Corner #1. Keep things as square and flush as possible as you tighten the screw to snug up the corner.

MICRON

FRAME – Z RAILS – CORNER 3

CORNER #3 ASSEMBLY
Before adding the next A extrusion,
preload M3 nuts into the B extrusion
that is about to be enclosed, as shown.
It receives. Corner extrusion #3 will
install the same as the others, using an
M3x8 BHCS for the blind joint. Note
that the linear rail should face Corner
#2. Keep things as square and flush as
possible as you tighten the screw to
snug up the corner.

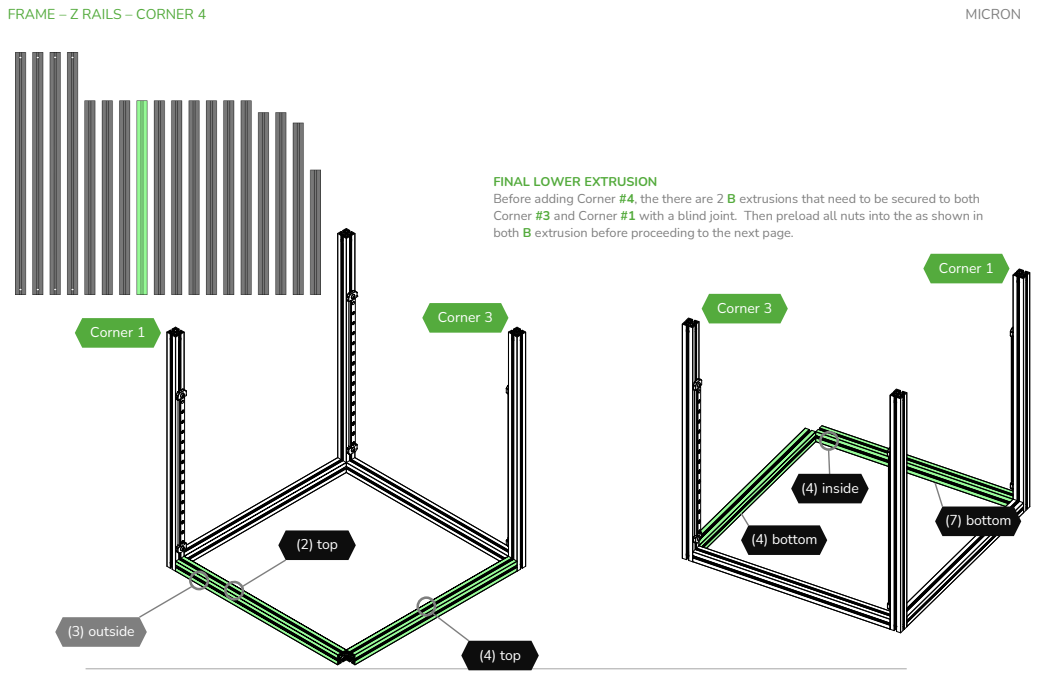
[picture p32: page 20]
(4) top; Corner 3; (2) top; (3) outside; (4) bottom; (7) bottom; (4) inside; MICRON; Corner 1

FRAME – Z RAILS – CORNER 4

FINAL LOWER EXTRUSION
Before adding Corner #4, the there are 2 B extrusions that need to be secured to both
Corner #3 and Corner #1 with a blind joint. Then preload all nuts into the as shown in
both B extrusion before proceeding to the next page.

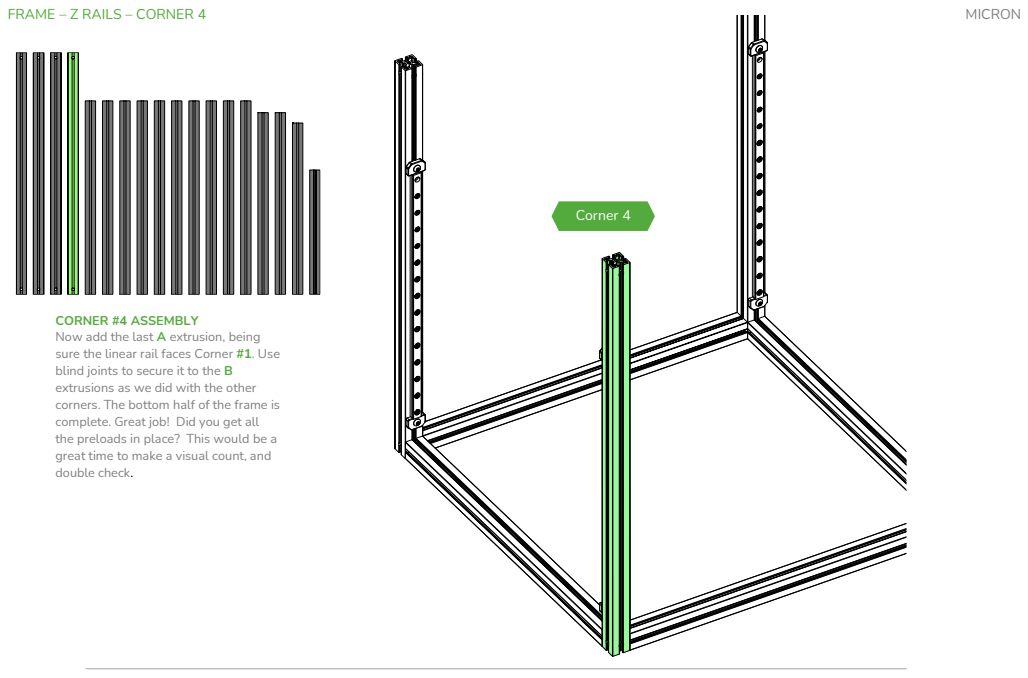
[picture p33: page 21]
Corner 4; MICRON

FRAME – Z RAILS – CORNER 4

CORNER #4 ASSEMBLY
Now add the last A extrusion, being
sure the linear rail faces Corner #1. Use
blind joints to secure it to the B
extrusions as we did with the other
corners. The bottom half of the frame is
complete. Great job! Did you get all
the preloads in place? This would be a
great time to make a visual count, and
double check.

FRAME – TOP EXTRUSIONS - 1

CAN YOU HANDLE IT?
Handles are an optional component you can install atop your Micron. They make
carrying the printer very easy. If you want to install handles that need preloaded
nuts now would be the time to add those.
Note: The default handles for Micron do not require preloaded nuts.

UPPER FRAME ASSEMBLY
The remaining four B extrusions will
install using blind joints, the same way
the lower ones were assembled. The
following pages will detail the
preloads for these extrusions, including
preloads for the optional handles.
Start with the extrusion that connects
Corners #1 and #4.

LIGHT IT UP
If you are planning to mount LEDs using
screws inside the enclosure, This is
where you would add the nuts for those.
In addition to the 4 already required.

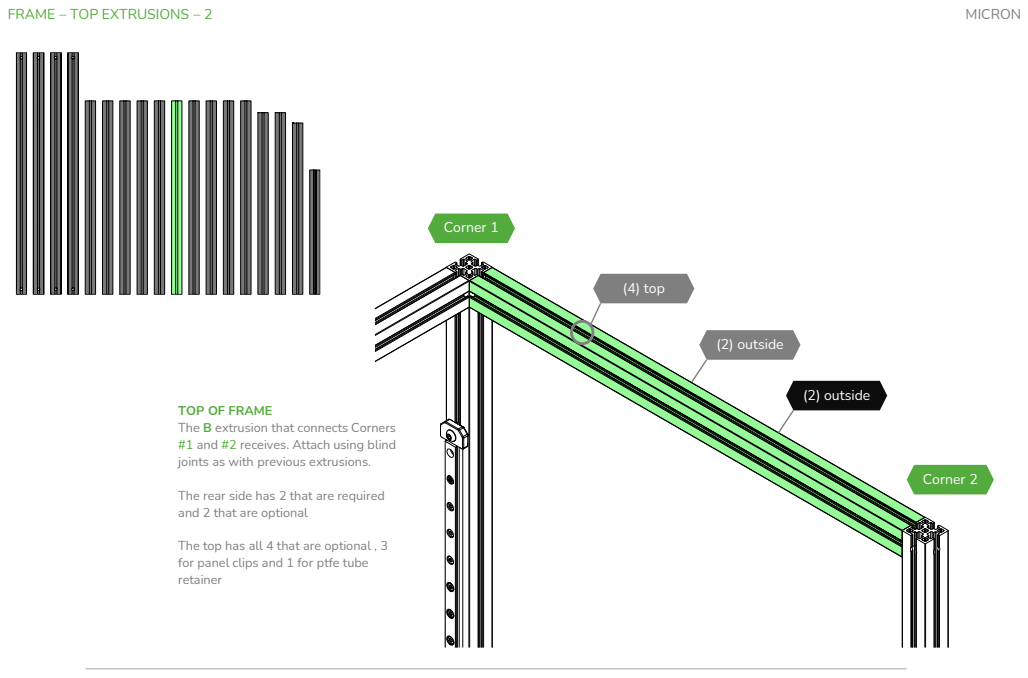
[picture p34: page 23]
Corner 1; Corner 2; (4) top; (2) outside; MICRON

FRAME – TOP EXTRUSIONS – 2

TOP OF FRAME
The B extrusion that connects Corners
#1 and #2 receives. Attach using blind
joints as with previous extrusions.

The rear side has 2 that are required
and 2 that are optional

The top has all 4 that are optional , 3
for panel clips and 1 for ptfe tube
retainer

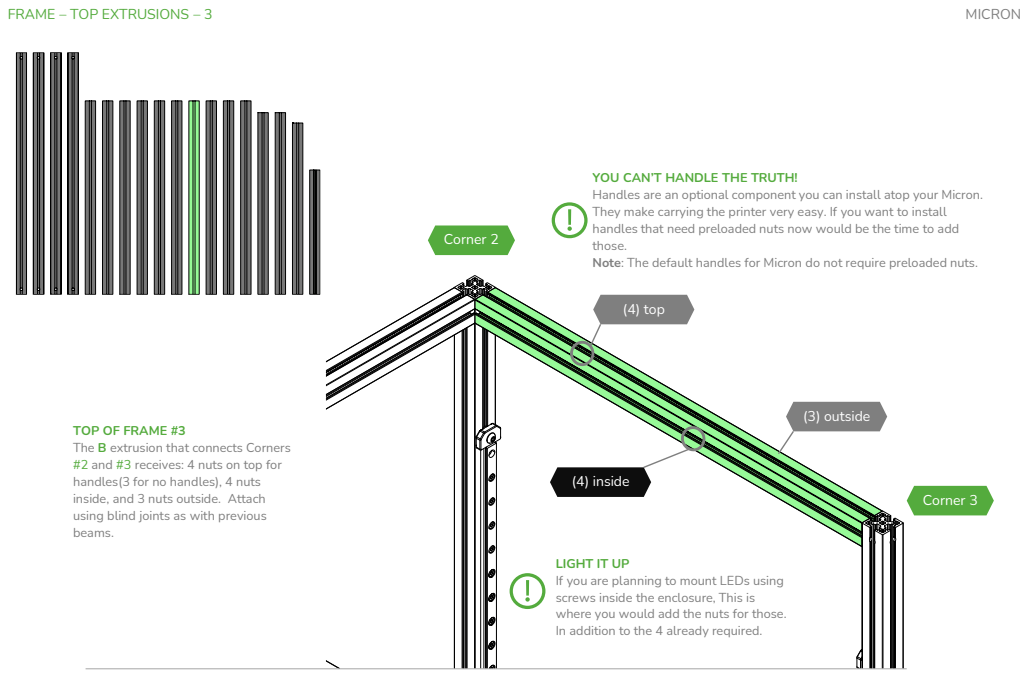
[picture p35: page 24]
Corner 2; Corner 3; (4) top; (3) outside; (4) inside; MICRON

FRAME – TOP EXTRUSIONS – 3

YOU CAN’T HANDLE THE TRUTH!
Handles are an optional component you can install atop your Micron.
They make carrying the printer very easy. If you want to install
handles that need preloaded nuts now would be the time to add
those.
Note: The default handles for Micron do not require preloaded nuts.

TOP OF FRAME #3
The B extrusion that connects Corners
#2 and #3 receives: 4 nuts on top for
handles(3 for no handles), 4 nuts
inside, and 3 nuts outside. Attach
using blind joints as with previous
beams.

LIGHT IT UP
If you are planning to mount LEDs using
screws inside the enclosure, This is
where you would add the nuts for those.
In addition to the 4 already required.

FRAME – TOP EXTRUSIONS – 4

(3) top TOP OF FRAME #4
Before placing the final B extrusion,
The final B extrusion itself receives an
optional 3 nuts on top.

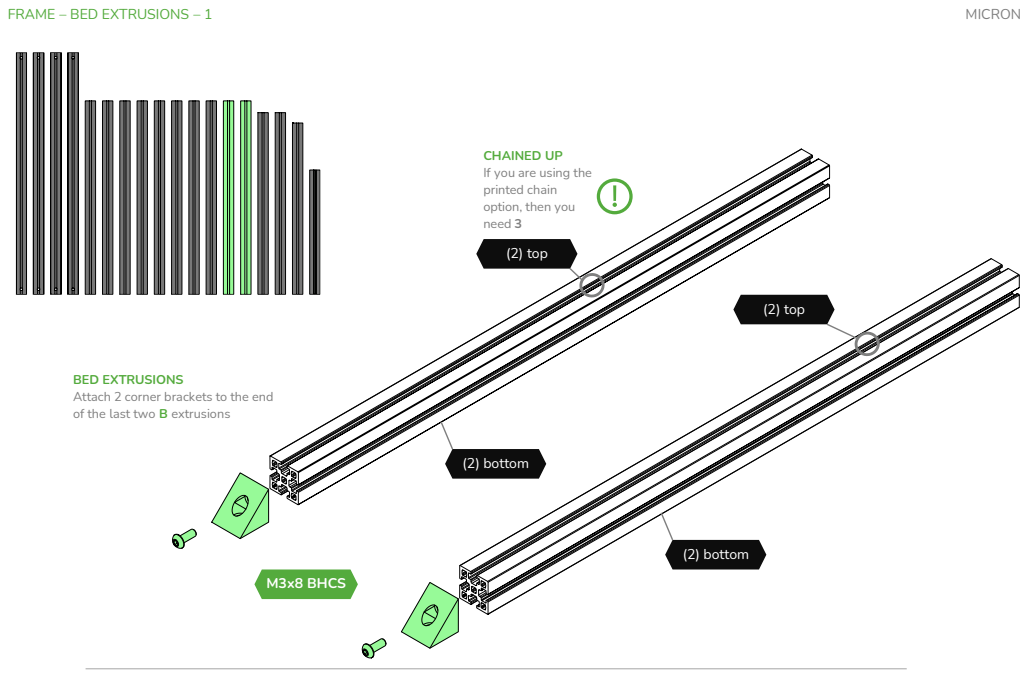
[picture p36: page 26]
FRAME – BED EXTRUSIONS – 1; MICRON; M3x8 BHCS; (2) top; (2) bottom

CHAINED UP
If you are using the
printed chain
option, then you
need 3
(2) top

BED EXTRUSIONS
Attach 2 corner brackets to the end
of the last two B extrusions

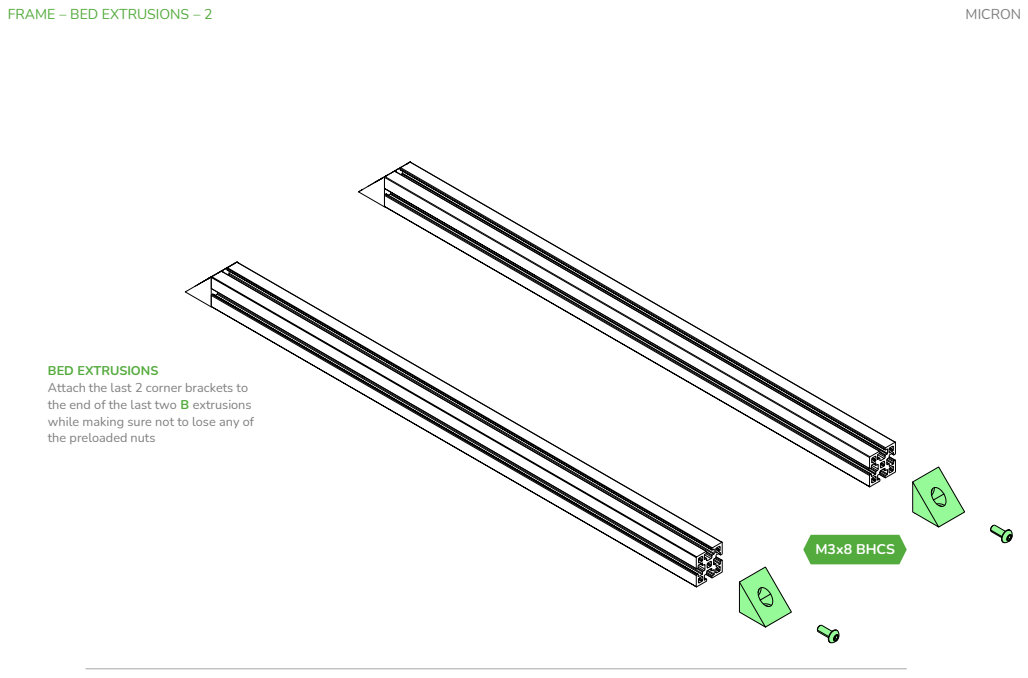
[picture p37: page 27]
FRAME – BED EXTRUSIONS – 2; MICRON; M3x8 BHCS

BED EXTRUSIONS
Attach the last 2 corner brackets to
the end of the last two B extrusions
while making sure not to lose any of
the preloaded nuts

FRONT - BED EXTRUSIONS
Mount the bed extrusions as shown,
running from the front to back in the
printer. Use the 2 middle nuts, of the 4
preloaded into the front . There should
be a single preloaded nut on the
outside of each B extrusion when done
for the Z belt hole covers. Don’t tighten
them down yet as the proper spacing
will be determined later.

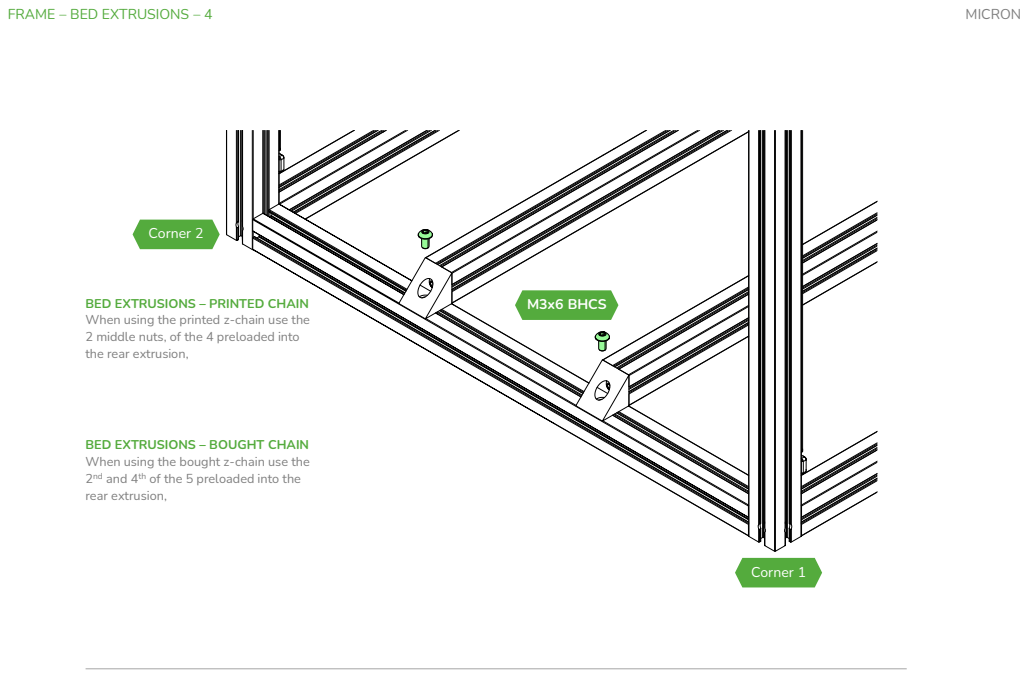
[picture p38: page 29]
FRAME – BED EXTRUSIONS – 4; MICRON; M3x6 BHCS; Corner 1; Corner 2

BED EXTRUSIONS – PRINTED CHAIN
When using the printed z-chain use the
2 middle nuts, of the 4 preloaded into
the rear extrusion,

BED EXTRUSIONS – BOUGHT CHAIN
When using the bought z-chain use the
rear extrusion,

nd and 4th of the 5 preloaded into the

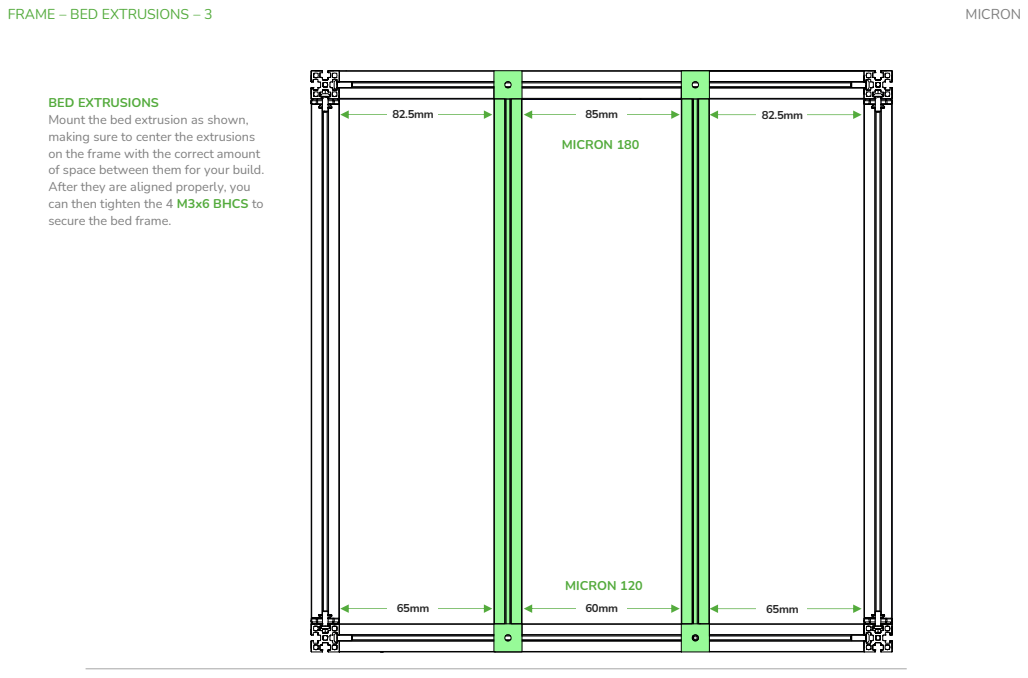
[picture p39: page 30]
FRAME – BED EXTRUSIONS – 3; MICRON; MICRON 180; MICRON 120

BED EXTRUSIONS
Mount the bed extrusion as shown,
making sure to center the extrusions
on the frame with the correct amount
of space between them for your build.
After they are aligned properly, you
can then tighten the 4 M3x6 BHCS to
secure the bed frame.

DECK PANEL
Install the deck panel , using 4 M3x8 BHCS.
Depending on the thickness of the panel you
may or may not need washers under the
screws

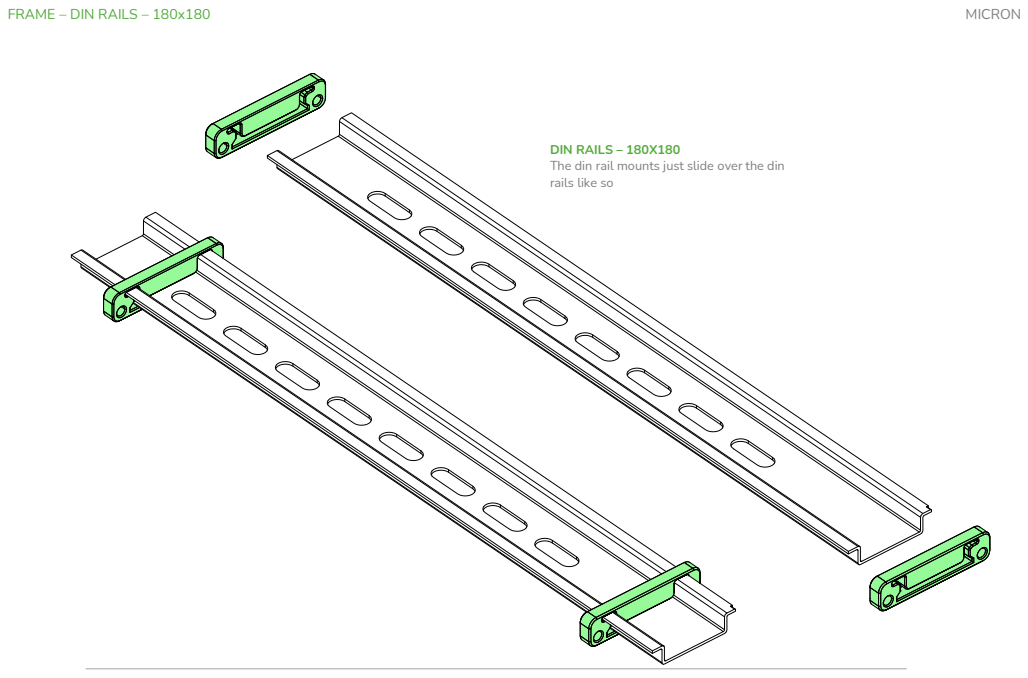
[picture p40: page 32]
FRAME – DIN RAILS – 180x180; MICRON

DIN RAILS – 180X180
The din rail mounts just slide over the din
rails like so

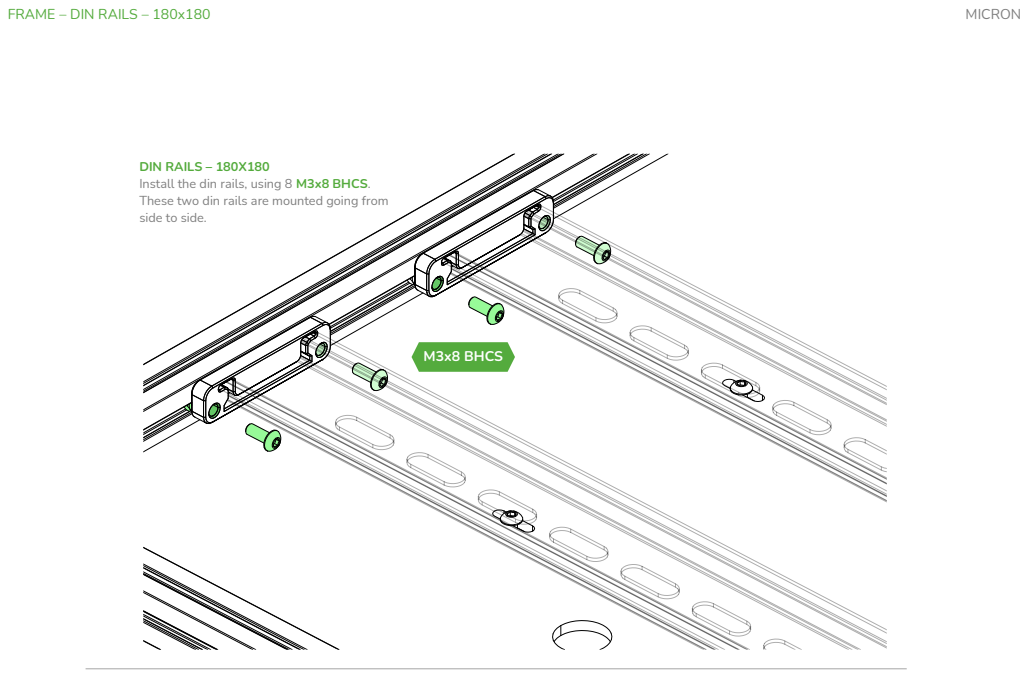
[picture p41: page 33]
FRAME – DIN RAILS – 180x180; MICRON; M3x8 BHCS

DIN RAILS – 180X180
Install the din rails, using 8 M3x8 BHCS.
These two din rails are mounted going from
side to side.

DIN RAILS – 180X180
Install the din rails, using 8 M3x8 BHCS.
These two din rails are mounted going from
side to side on the other side of the frame.

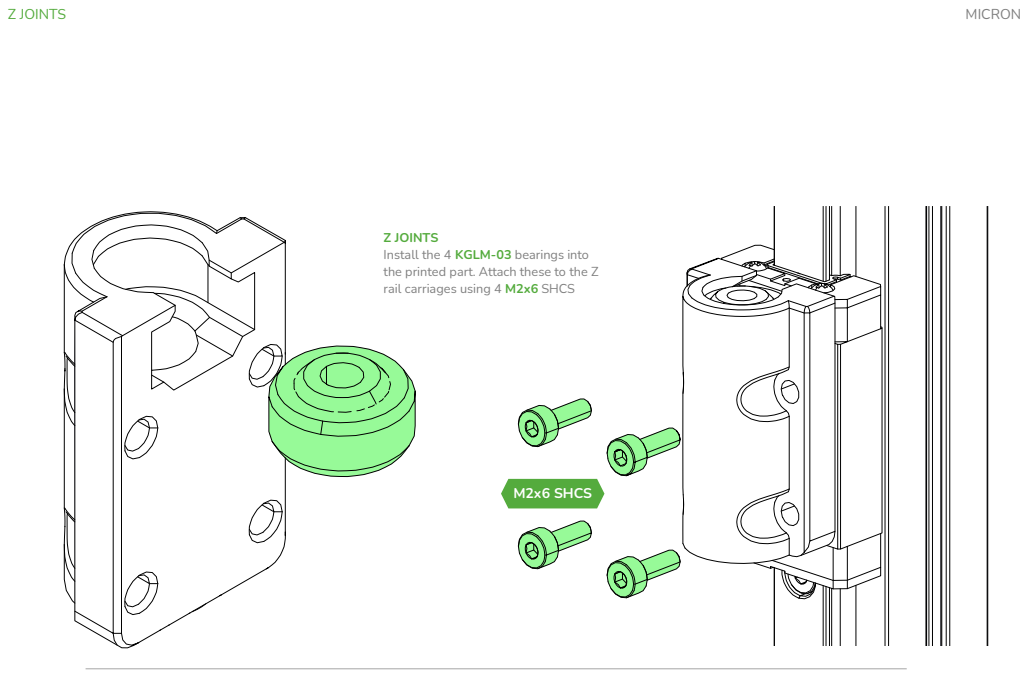
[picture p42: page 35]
Z JOINTS; MICRON; M2x6 SHCS

Z JOINTS
Install the 4 KGLM-03 bearings into
the printed part. Attach these to the Z
rail carriages using 4 M2x6 SHCS

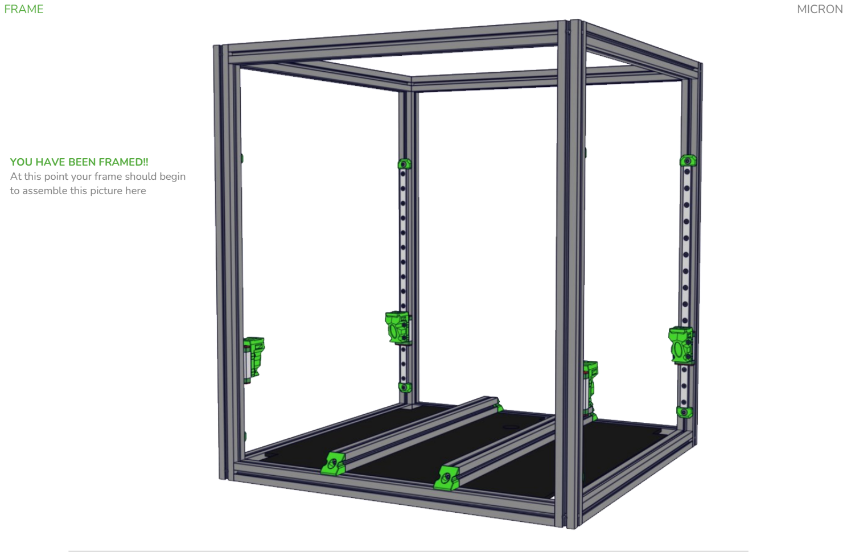
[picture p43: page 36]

FRAME | MICRON

YOU HAVE BEEN FRAMED!!
At this point your frame should begin to assemble this picture here

BELTED Z DRIVES | MICRON

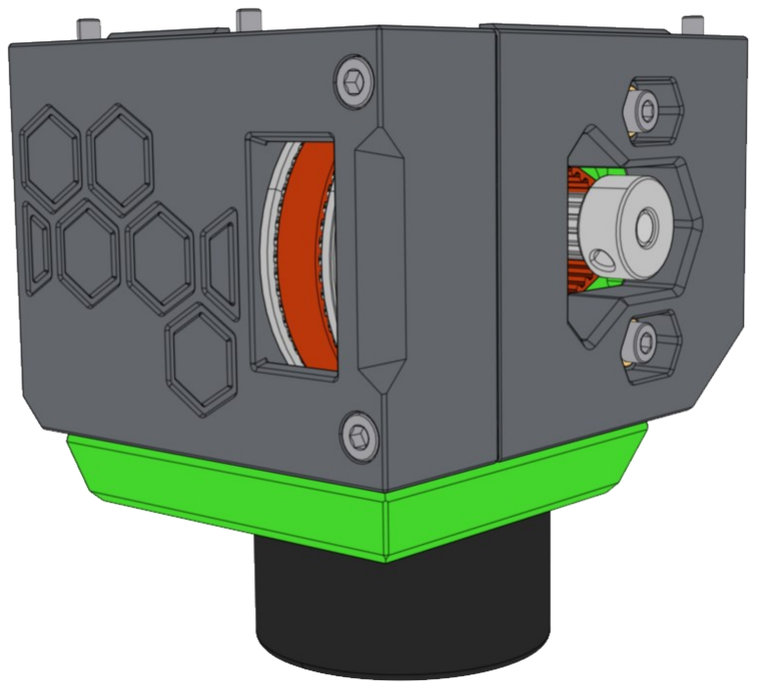
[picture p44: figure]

Z JOINTS | MICRON

Z JOINTS | MICRON

Z JOINTS | MICRON

Z JOINTS | MICRON

Z JOINTS | MICRON

Z JOINTS | MICRON

Z JOINTS | MICRON

Z JOINTS | MICRON

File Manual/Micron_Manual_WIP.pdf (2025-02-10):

ASSEMBLY MANUAL
Everything is smaller but the price.

TABLE OF CONTENTS

INTRODUCTION | MICRON

## STL FILE KEY

## PRINT GUIDELINES

The STL naming convention used for Micron is the same as that used for VORON printers:

The recommended print settings are also those used for VORON printers:

### PRIMARY COLOR

Example
z_drive_main_a_x2.stl
These files will have nothing at the start of the filename.

### ACCENT COLOR

Example
[a]_z_motor_mount_a_x2.stl These files will have ‘’[a]’’ to the front to mention that they are intended to be printed with an accent color.

### QUANTITY REQUIRED

Example
[a]_z_motor_mount_a_x2.stl If a file ends with ‘’_x#’’, that is telling you the quantity of that part required to build this system..

FDM MATERIAL
Micron was designed for ABS. Use other plastics at your own discretion.
LAYER HEIGHT
Recommended : 0.2mm
EXTRUSION WIDTH
Recommended : Forced 0.4mm INFILL PERCENTAGE
Recommended : 40%

INFILL TYPE
Grid, Gyroid, Honeycomb, Triangle, Cubic, Adaptive Cubic.
WALL COUNT
Recommended : 4
SOLID TOP/BOTTOM LAYERS
Recommended : 5
SUPPORTS REQUIRED
If the part needs supports, they are built into the model.
INTRODUCTION | MICRON

HOW TO GET HELP

If you need assistance with your build you can head over the DOOMCUBE Discord server and post your questions ( typically in the #micron_build_questions channel ). It is the primary help channel for the Micron! You can also check the Github page for the latest releases.

DISCO? OH …DISCORD
If you need assistance with your build you can head over the DOOMCUBE Discord server and post your questions ( typically in the #micron_build_questions channel ). It is the primary help channel for the Micron!

GIT GUD
If you want to stay up to date on the latest files for Micron. The github page is the only source for the latest files.
HARDWARE - REFERENCES | MICRON

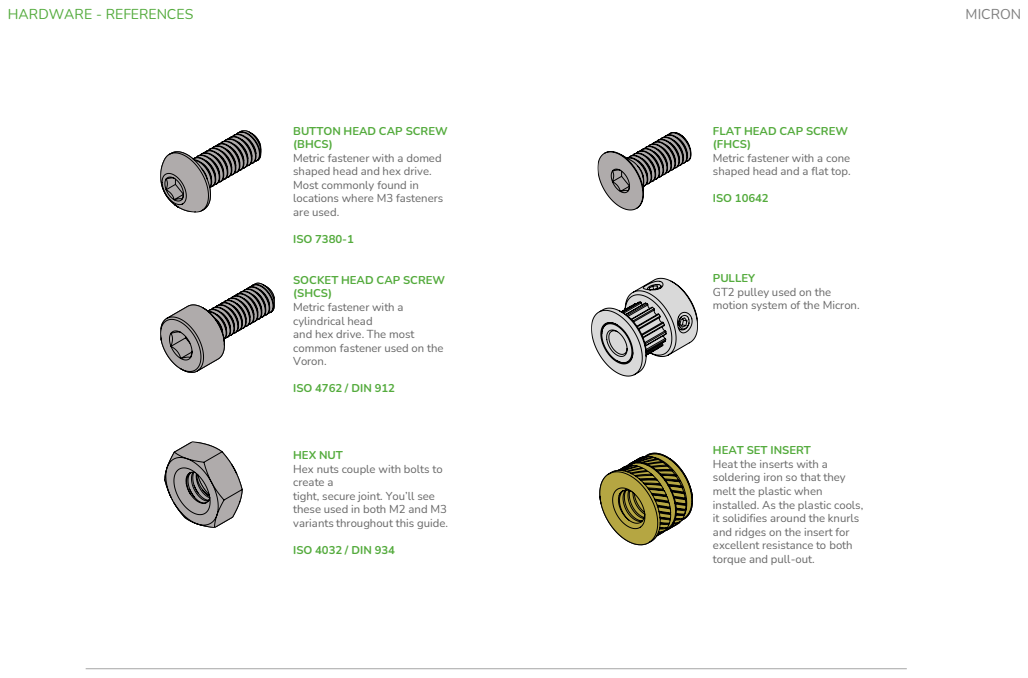
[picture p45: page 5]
HARDWARE - REFERENCES; MICRON

BUTTON HEAD CAP SCREW
(BHCS)
Metric fastener with a domed
shaped head and hex drive.
Most commonly found in
locations where M3 fasteners
are used.
ISO 7380-1

FLAT HEAD CAP SCREW
(FHCS)
Metric fastener with a cone
shaped head and a flat top.
ISO 10642

SOCKET HEAD CAP SCREW
(SHCS)
Metric fastener with a
cylindrical head
and hex drive. The most
common fastener used on the
Voron.
ISO 4762 / DIN 912

PULLEY
GT2 pulley used on the
motion system of the Micron.

HEAT SET INSERT
Heat the inserts with a
soldering iron so that they
melt the plastic when
installed. As the plastic cools,
it solidifies around the knurls
and ridges on the insert for
excellent resistance to both
torque and pull-out.

HEX NUT
Hex nuts couple with bolts to
create a
tight, secure joint. You’ll see
these used in both M2 and M3
variants throughout this guide.
ISO 4032 / DIN 934

SELF TAPPING SCREW
Fastener with a pronounced thread profile that is screwed directly into plastic.

M3 SHIMS
Not to be confused with
stamped washers. These are used in all M3 call-out
locations in this manual.
3x6x0.5 DIN 988

5mm x 47mm Shaft
Steel shaft, 5mm in diameter, 47mm long with a flat ground on it used in the Z drive gear box assembly

F623 BEARING
A ball bearing with a flange used in various gantry
locations.

625 BEARING
A ball bearing with used in the Z drive.

MICRON Logo
Look for Micron Logo next to the printed part, this is a direct link to the file on the github repo.

ATTENTION BUBBLE
This logo denotes steps that are common areas that
mistakes can occur.

HARDWARE - REFERENCES

Hardware Used

Look for the GREEN call outs to mention the various hardware used

(qty) location - SIZE

Look for the BLACK call outs to mention the preloaded M3 nuts, NOTE: some of them are specific to the size of printer and will be in bold at the end

MICRON

BLIND JOINT BASICS
Blind Joints provide a cost-effective and rigid
assembly method.
The head of the BHCS is slid into the channel of
another extrusion and securely fastened through
a small access hole in the extrusion.
If you’ve never assembled one before we
recommend you watch the linked guide.

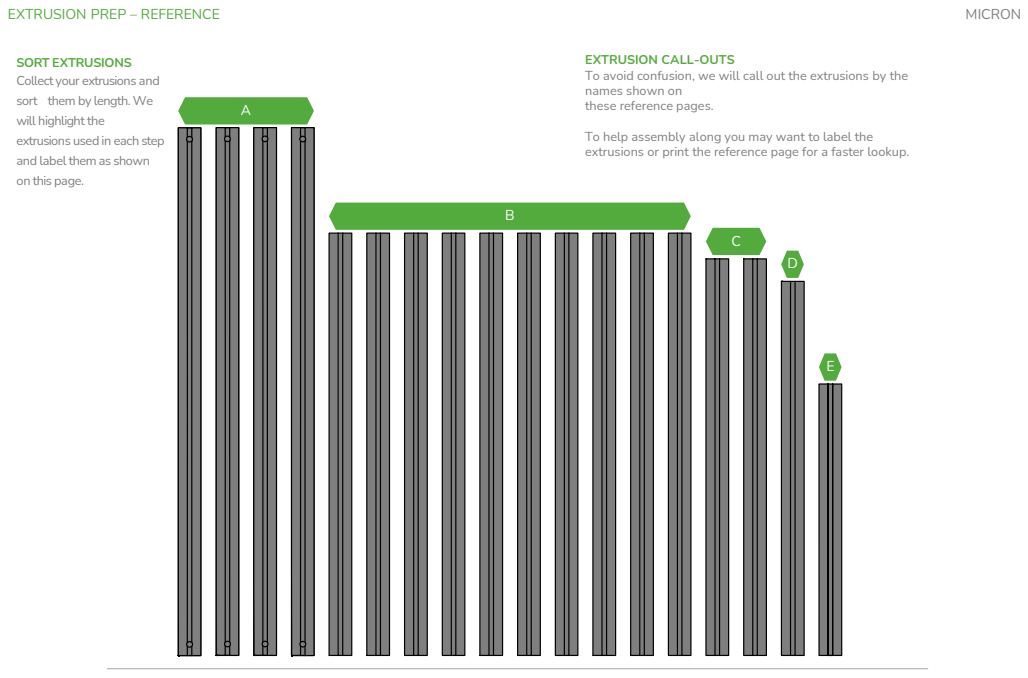
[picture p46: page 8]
EXTRUSION PREP – REFERENCE; MICRON

SORT EXTRUSIONS
Collect your extrusions and
sort them by length.We
will highlight the
extrusions used in each step
and label them as shown
on this page.

EXTRUSION CALL-OUTS
To avoid confusion, we will call out the extrusions by the
names shown on
these reference pages.
To help assembly along you may want to label the
extrusions or print the reference page for a faster lookup.

BED EXTRUSIONS?
Some frame kits come with bed
extrusions that are mounted using
blind joints. These will end up being 2
longer extrusions and 8 B extrusions.

MULTIPLE VIEWS
The views shown are the left, front, right, and
bottom views of each extrusion.

EXTRUSION PREP – REFERENCE – 120x120

ALL UNITS ARE METRIC
If a unit is not specified
assume it’s metric.

MULTIPLE VIEWS
The views shown are the left, front, right, and
bottom views of each extrusion.

PREPARE 8 EXTRUSIONS
These extrusions are going to be used in
this section. Prepare them as shown above
by partially threading in an M3x8 BHCS
in either side.

POPULATING NUT CARRIERS
Pictured shows all the m2 nuts populated, but depending on how much M2 hardware you sourced, you may not be able to fully populate the M2 Nut Adapters if that happens, skipping

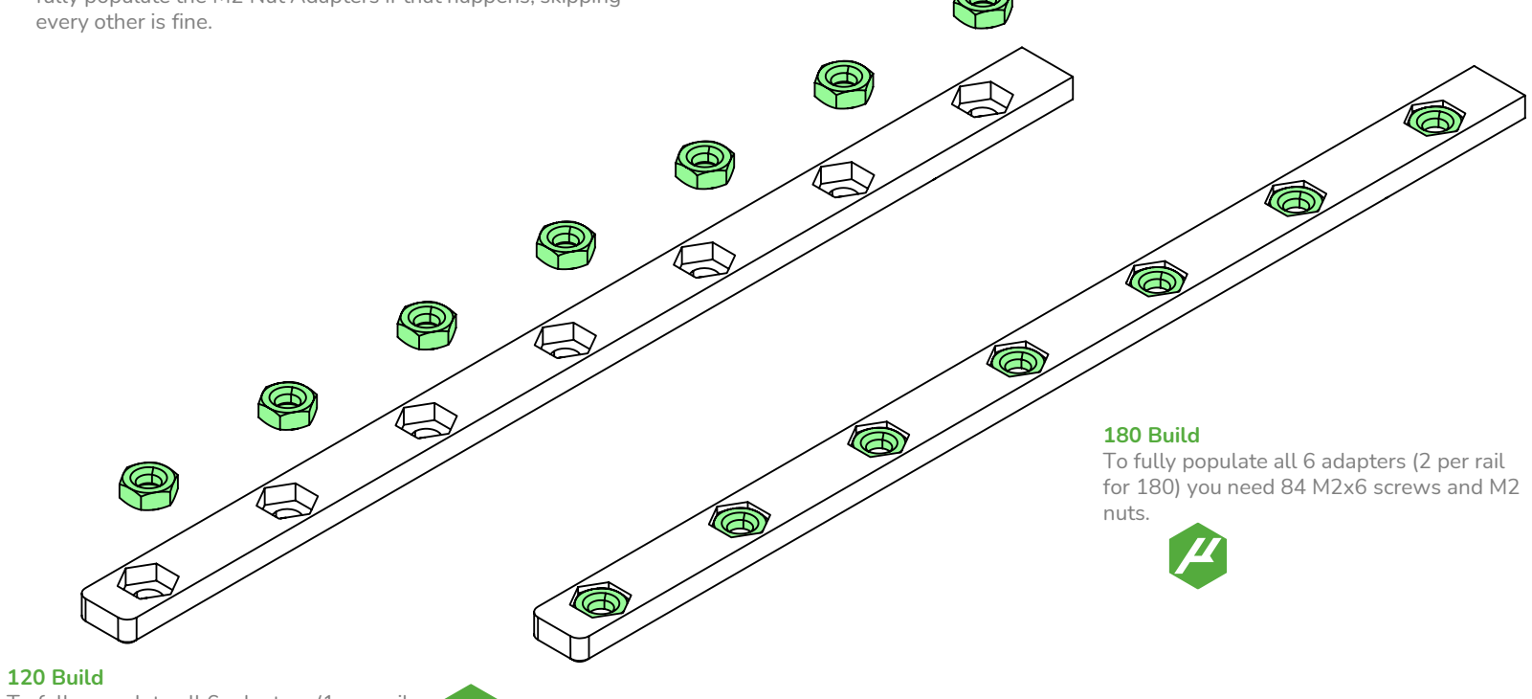
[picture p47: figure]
every other is fine.; 180 Build; for 180) you need 84 M2x6 screws and M2 nuts.; 120 Build

To fully populate all 6 adapters (2 per rail

To fully populate all 6 adapters (1 per rail for 120) you need 60 M2x6 screws and M2 nuts.

FRAME – Z RAILS | MICRON

M2x6 SHCS

M2 Hex Nut

Z RAILS ALIGNMENT

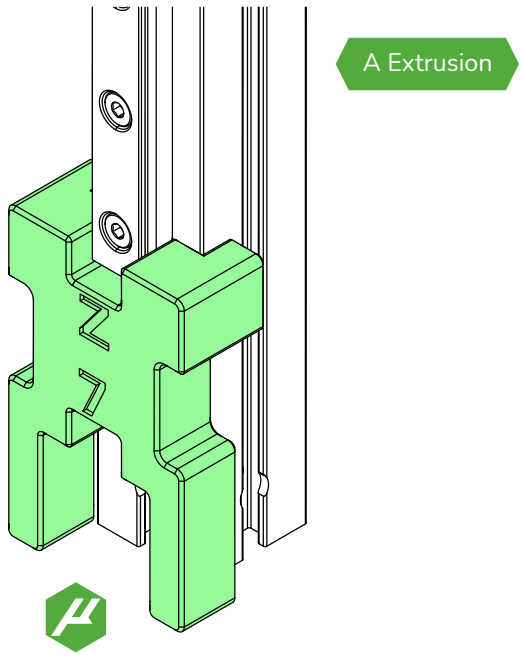
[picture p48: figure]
A Extrusion

Z rails are mounted before assembly of the frame. Stand up one of the A extrusions and use the printed rail alignment tool as shown to align the bottom of the rail. The rail end should be 36mm from the bottom of the extrusion. Use a second rail alignment tool on the upper half of the rail, using the section marked ‘7’, to properly center the rail on the extrusion. Tighten the screws, being careful to maintain the alignment provided by the printed tools. Repeat this process for all 4 A extrusions and their rails.

FRAME – Z RAILS | MICRON

RAIL STOPS
With the Z rails installed, the rail stops can now be added to both ends. Loosely screw an M3x8 BHCS. Repeat for both ends of all 4 Z rails. Now you can work on the build without risking a Z carriage flying off its rail.

WHERE’S THE NUT!?
The instructions won’t call out nuts that were inserted in a previous step, nor nuts that can be easily inserted in the current step. if a screw does NOT thread into a nut we will explicitly state this. You can assume that all screws that enter extrusion slots thread into a nut.
FRAME – Z RAILS | MICRON

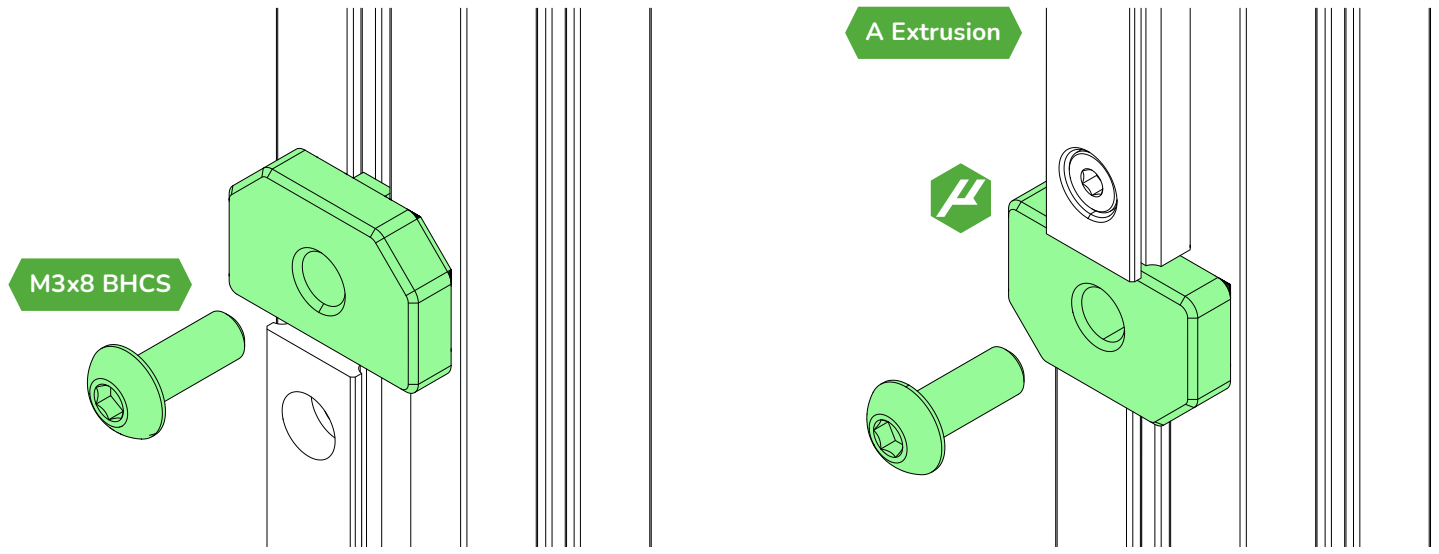
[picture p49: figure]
M3x8 BHCS; A Extrusion
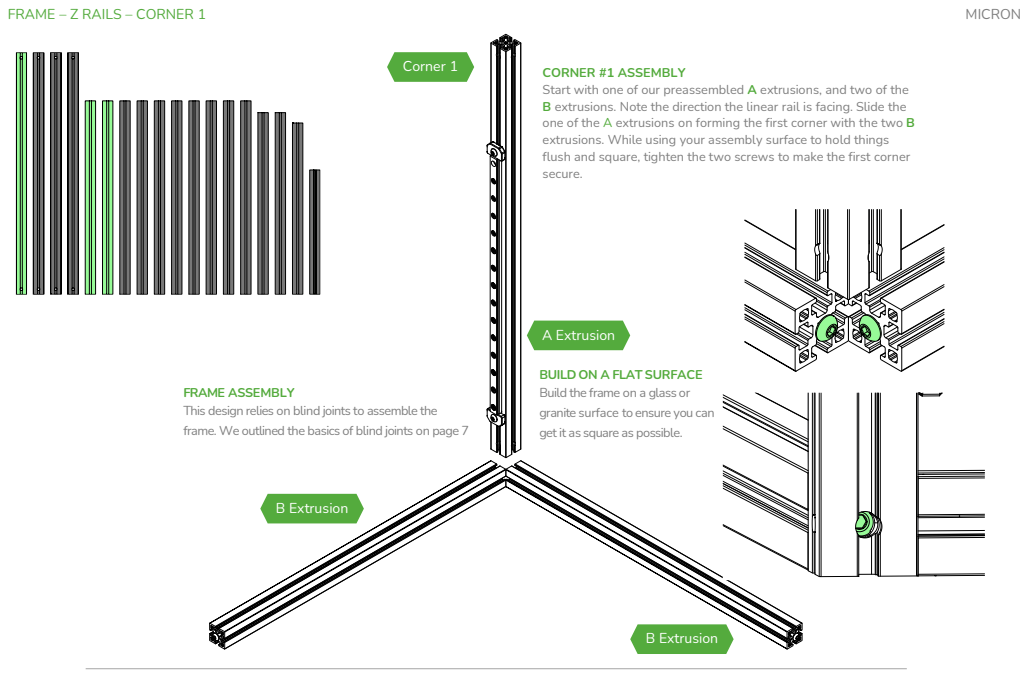
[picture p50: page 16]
B Extrusion; A Extrusion; Corner 1; MICRON

FRAME – Z RAILS – CORNER 1

CORNER #1 ASSEMBLY
Start with one of our preassembled A extrusions, and two of the
B extrusions. Note the direction the linear rail is facing. Slide the
one of the A extrusions on forming the first corner with the two B
extrusions. While using your assembly surface to hold things
flush and square, tighten the two screws to make the first corner
secure.

BUILD ON A FLAT SURFACE
Build the frame on a glass or
granite surface to ensure you can
getit as square as possible.

FRAME ASSEMBLY
This design relies on blind joints to assemble the
frame. We outlined the basics of blind joints on page 7

FRAME – Z RAILS – CORNER 2

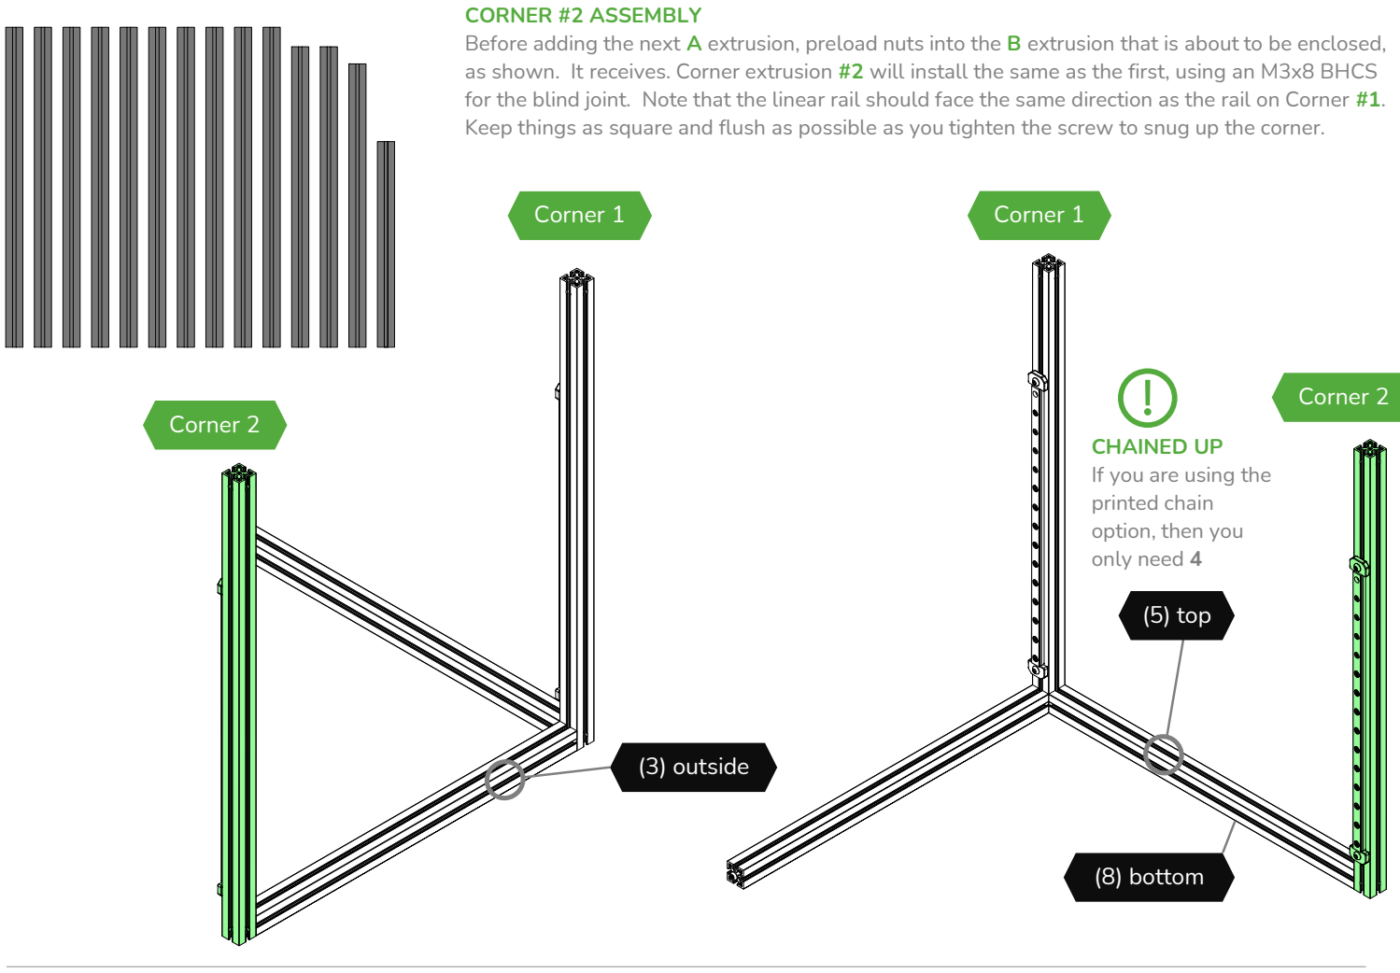
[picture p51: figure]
(5) top; (3) outside; (8) bottom; CORNER #2 ASSEMBLY; Corner 2; Corner 1; CHAINED UP If you are using the printed chain option, then you only need 4

Before adding the next A extrusion, preload nuts into the B extrusion that is about to be enclosed, as shown. It receives. Corner extrusion #2 will install the same as the first, using an M3x8 BHCS for the blind joint. Note that the linear rail should face the same direction as the rail on Corner #1. Keep things as square and flush as possible as you tighten the screw to snug up the corner.

MICRON

FRAME – Z RAILS – CORNER 3

CORNER #3 ASSEMBLY
Before adding the next A extrusion,
preload M3 nuts into the B extrusion
that is about to be enclosed, as shown.
It receives. Corner extrusion #3 will
install the same as the others, using an
M3x8 BHCS for the blind joint. Note
that the linear rail should face Corner
#2. Keep things as square and flush as
possible as you tighten the screw to
snug up the corner.

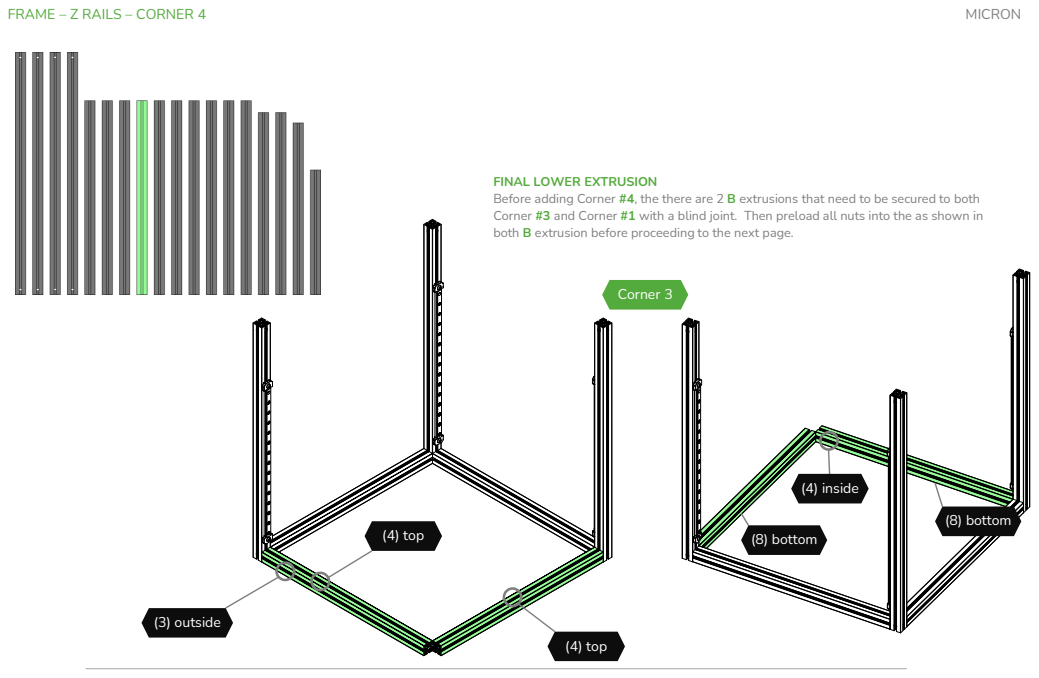
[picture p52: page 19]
(4) top; Corner 3; (3) outside; (8) bottom; (4) inside; MICRON

FRAME – Z RAILS – CORNER 4

FINAL LOWER EXTRUSION
Before adding Corner #4, the there are 2 B extrusions that need to be secured to both
Corner #3 and Corner #1 with a blind joint. Then preload all nuts into the as shown in
both B extrusion before proceeding to the next page.

FRAME – Z RAILS – CORNER 4

CORNER #4 ASSEMBLY
Now add the last A extrusion, being
sure the linear rail faces Corner #1. Use
blind joints to secure it to the B
extrusions as we did with the other
corners. The bottom half of the frame is
complete. Great job! Did you get all
the preloads in place? This would be a
great time to make a visual count, and
double check.

FRAME – TOP EXTRUSIONS - 1

CAN YOU HANDLE IT?
Handles are an optional component
you can install atop your Micron. They
make carrying the printer very easy. If
you want to install handles now would
be the time to preload any addition
nuts need.

UPPER FRAME ASSEMBLY
The remaining four B extrusions will
install using blind joints, the same way
the lower ones were assembled. The
following pages will detail the
preloads for these extrusions, including
preloads for the optional handles.
Start with the extrusion that connects
Corners #1 and #4.

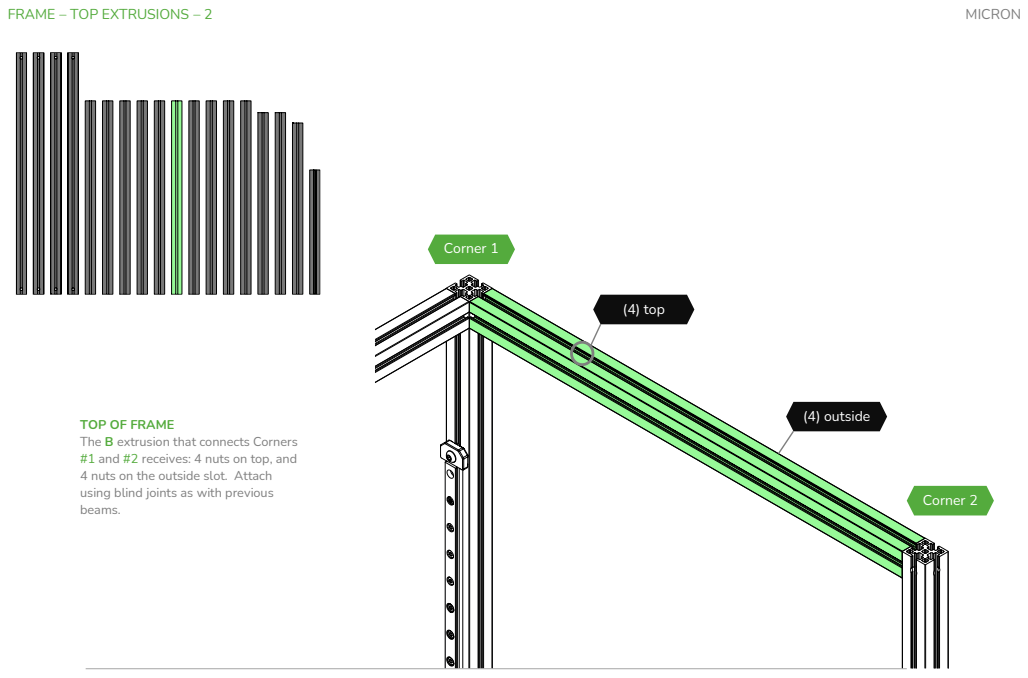
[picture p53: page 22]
Corner 1; Corner 2; (4) top; MICRON

FRAME – TOP EXTRUSIONS – 2

(4) outside TOP OF FRAME
The B extrusion that connects Corners
#1 and #2 receives: 4 nuts on top, and
4 nuts on the outside slot. Attach
using blind joints as with previous
beams.

FRAME – TOP EXTRUSIONS – 3

YOU CAN’T HANDLE THE TRUTH!
Handles are an optional component
you can install atop your Micron. They
make carrying the printer very easy. If
you want to install handles now would
be the time to preload any addition
nuts need.

TOP OF FRAME #3
The B extrusion that connects Corners
#2 and #3 receives: 4 nuts on top for
handles(3 for no handles), 4 nuts
inside, and 3 nuts outside. Attach
using blind joints as with previous

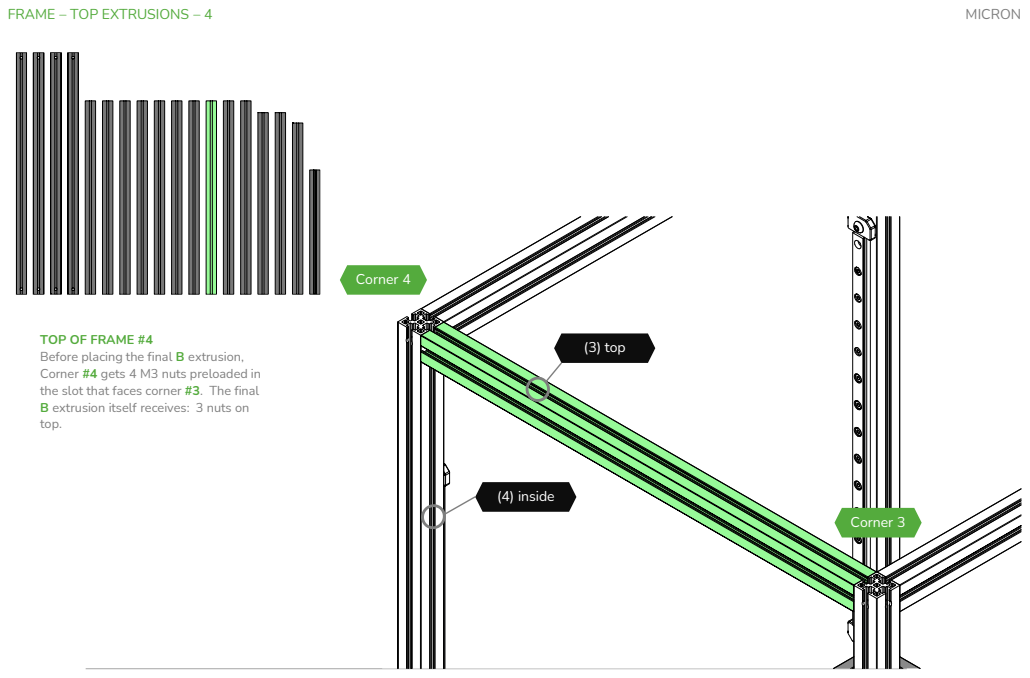
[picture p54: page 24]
Corner 3; Corner 4; (3) top; (4) inside; MICRON

FRAME – TOP EXTRUSIONS – 4

TOP OF FRAME #4
Before placing the final B extrusion,
Corner #4 gets 4 M3 nuts preloaded in
the slot that faces corner #3. The final
B extrusion itself receives: 3 nuts on
top.

CHAINED UP
If you are using the
printed chain
option, then you
need 3
(2) top

BED EXTRUSIONS
Attach 2 corner brackets to the end
of the last two B extrusions

BED EXTRUSIONS
Attach the last 2 corner brackets to
the end of the last two B extrusions
while making sure not to lose any of
the preloaded nuts

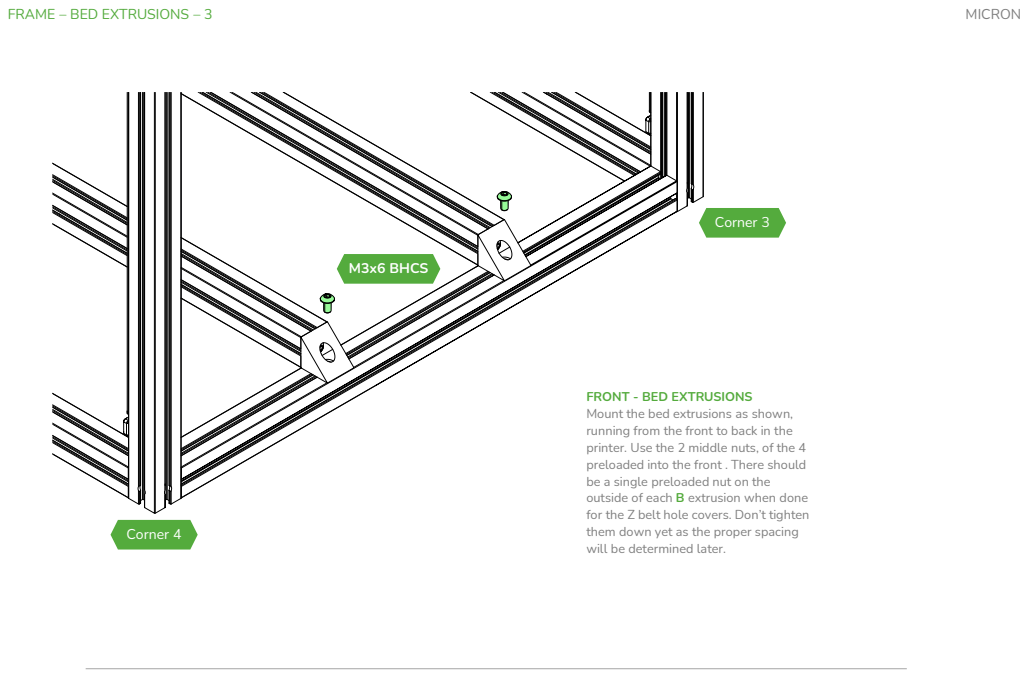
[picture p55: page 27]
FRAME – BED EXTRUSIONS – 3; MICRON; M3x6 BHCS; Corner 4; Corner 3

FRONT - BED EXTRUSIONS
Mount the bed extrusions as shown,
running from the front to back in the
printer. Use the 2 middle nuts, of the 4
preloaded into the front . There should
be a single preloaded nut on the
outside of each B extrusion when done
for the Z belt hole covers. Don’t tighten
them down yet as the proper spacing
will be determined later.

BED EXTRUSIONS – PRINTED CHAIN
When using the printed z-chain use the
2 middle nuts, of the 4 preloaded into
the rear extrusion,

BED EXTRUSIONS – BOUGHT CHAIN
When using the bought z-chain use the
rear extrusion,

nd and 4th of the 5 preloaded into the

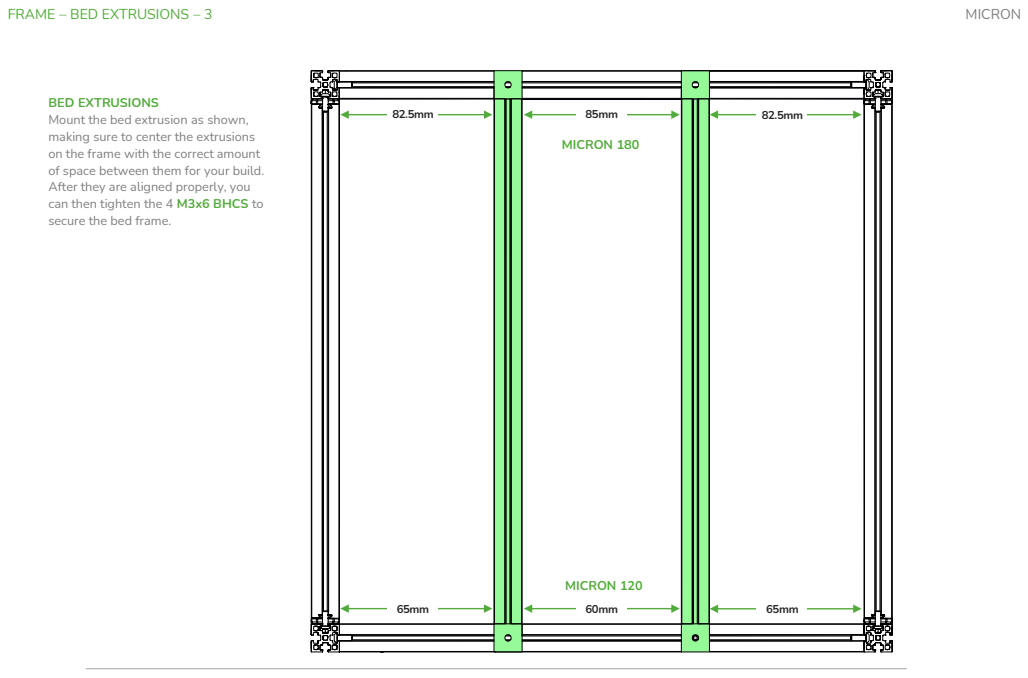
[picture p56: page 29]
FRAME – BED EXTRUSIONS – 3; MICRON; MICRON 180; MICRON 120

BED EXTRUSIONS
Mount the bed extrusion as shown,
making sure to center the extrusions
on the frame with the correct amount
of space between them for your build.
After they are aligned properly, you
can then tighten the 4 M3x6 BHCS to
secure the bed frame.

DECK PANEL
Install the deck panel , using 4 M3x8 BHCS.
Depending on the thickness of the panel you
may or may not need washers under the
screws

DIN RAILS – 180X180
The din rail mounts just slide over the din
rails like so

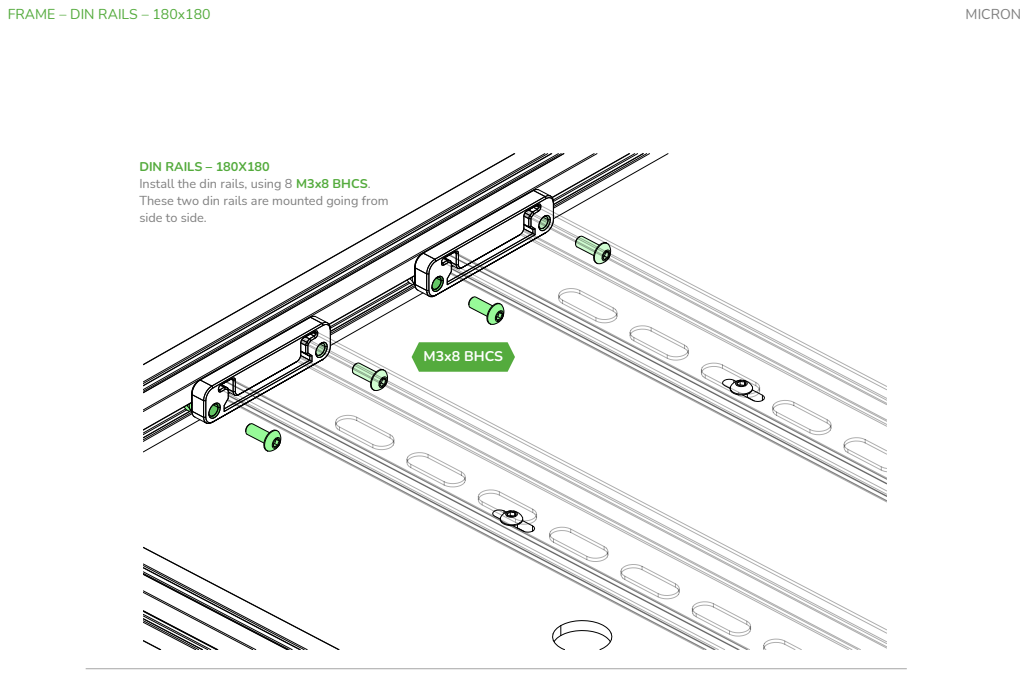
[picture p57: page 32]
FRAME – DIN RAILS – 180x180; MICRON; M3x8 BHCS

DIN RAILS – 180X180
Install the din rails, using 8 M3x8 BHCS.
These two din rails are mounted going from
side to side.

DIN RAILS – 180X180
Install the din rails, using 8 M3x8 BHCS.
These two din rails are mounted going from
side to side on the other side of the frame.

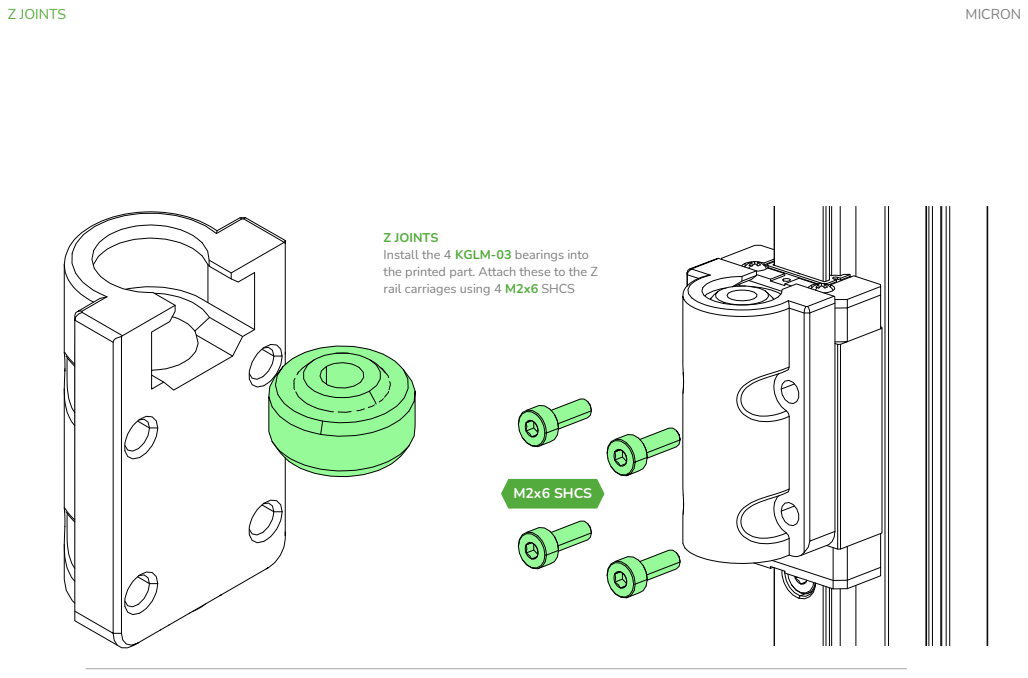
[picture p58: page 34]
Z JOINTS; MICRON; M2x6 SHCS

Z JOINTS
Install the 4 KGLM-03 bearings into
the printed part. Attach these to the Z
rail carriages using 4 M2x6 SHCS

YOU HAVE BEEN FRAMED!!
At this point your frame should begin
to assemble this picture here

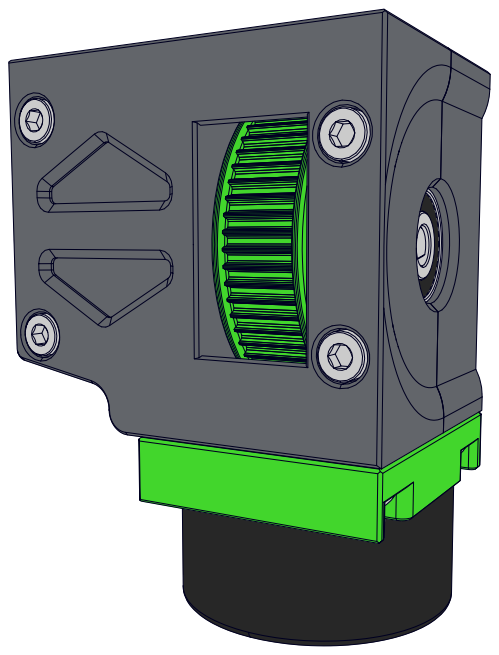
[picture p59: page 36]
BELTED Z DRIVES; MICRON

Z DRIVES PULLEYS | MICRON

WHICH PULLEY?
Before you start the shaft assembly, make sure to measure the length of your GT2-16T pulleys. There are 2 different lengths. The length will determine how you assemble the shaft assembly, and which printed spacers to use.

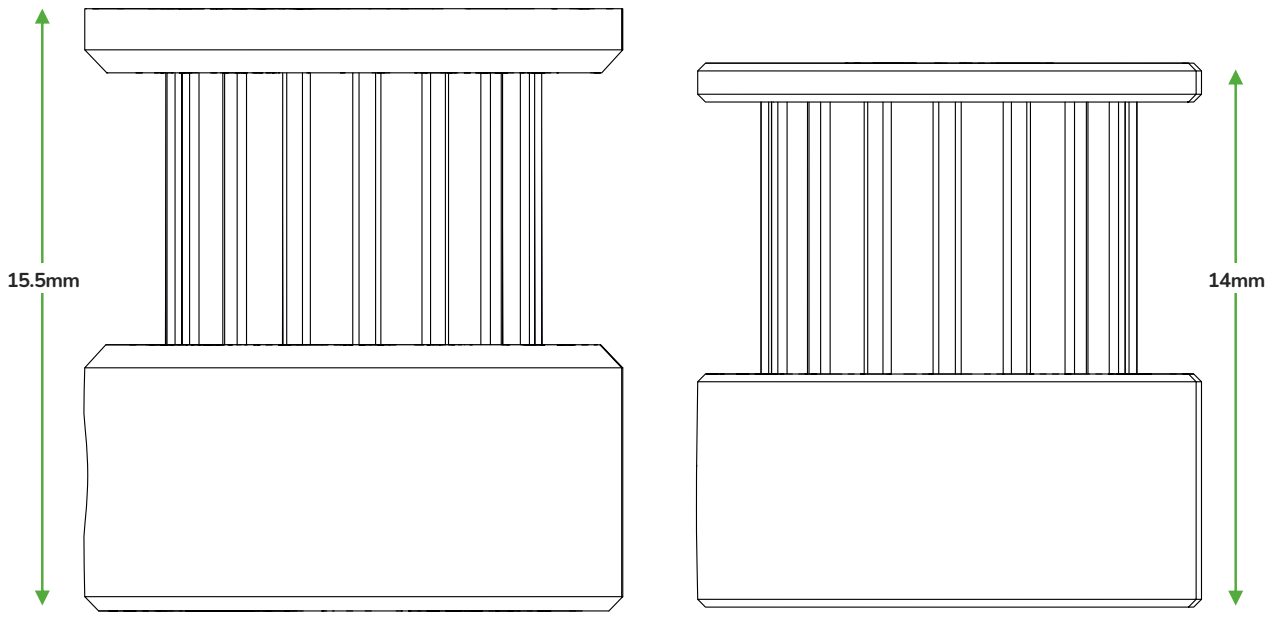
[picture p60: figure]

DEFLANGING PULLEY
To start assembly of the Belted Z
drives you will start by removing the
top flange from x4 of the GT2-16T
pulleys. To do this, you can use a pair
of pliers and pull the top flange off the
pulley.

Z DRIVE SHAFT ASSEMBLY | MICRON

625 Bearing; GT2-16T De-Flanged; SPACERS!!; are needed.; Spacer_B; ABC..EASY AS 123; pulley; GRUB SCREWS? Its always the grub screws….don’t forget to Loctite the grub screws so they don’t come loose. Most issues on V2.4 and Micron Z drives are because of loose grub screws; Spacer_A; Spacer_C

Based on which size your GT2-16T is this will determine which spacers

The spacers are labeled A,B, and C. If you have the 15.5mm pulleys, then you don’t have a C spacer. The manual will be using the 14mm long

Z DRIVE SHAFT ASSEMBLY

ASSEMBLING THE 64T PULLEY
The printed pulley has a flat side and a concave side.
The de-flanged pulley slides into the concave side of
the printed pulley and is secured from the flat side with
4 M3x6 grub screws.

Z DRIVE ASSEMBLY; MICRON; M3 Heatset

Z DRIVE ASSEMBLY
Begin by installing the heatset inserts into the Z drive
parts. Each pair of Z drive halves has a total of 8
required heatsets, as shown in the illustrations below. If
you are building a 180, the you only need 7. The darker
green one isn’t needed if building a 180

Z MOTOR PULLEY ASSEMBLY | MICRON

Z MOTOR PULLEY
To continue with the Z drive assembly, attach a GT2 16T pulley as shown to each of the 4 Z motors. Tighten one of the set screw just tight enough to keep the pulleys from falling off. DO NOT USE LOCTITE AT THIS POINT! We will determine the precise positioning of these pulleys once the motors are mounted to the printer. For now, we are just putting the pulleys in place, so we don’t have to slide them on to mounted motors.

Z DRIVE SECURING
secure the 2 halves of the Z drive assembly with 4
screws ensuring the belt is in the correct place.

Z DRIVE BELT
Add the GT2-188t belt loop around the 64T pulley
before closing it off.

Z MOTOR MOUNT; MICRON; M3x8 BHCS

Z MOTOR MOUNT
Z motor mount is best used with the wires for the z to
be facing down or towards the inside of the printer
Note: The motor is on a slight angle in relation to the
motor mount.

FEET ASSEMBLY
To assembly the Z drive cap / feet, you need to insert an
M5 nut into the drive cover and attach it to the Z drive
with 3 M3x8 BHCS screws.

Z DRIVE MOUNT
Z Drive is mounted using two M3x40 SHCS.
If you installed the printed NDN nut holder
then this is where you will use that to secure
the drive housing.

Z MOTOR MOUNTING | MICRON

M3x8 BHCS

PRELOAD POSITIONS
Before installing the Z motors, take note of the 8 preloaded nuts in the slot to which we are mounting them. 4 of these nuts will be used to mount the Z motors. The position of the remaining 4 nuts is critical to finishing the assembly. When you have the motors mounted, you want one nut between each motor and its Z drive, and two nuts in the center, between the two motors. These 4 nuts will be used to secure the skirts later in the assembly.

Z MOTOR MOUNTING
Using 2 M3x8 BHCS attach the Z motor. This is when you will tension the 188 tooth belt loop.

Z IDLERS; MICRON

Z TENSIONER
Slide the tensioner into the main body
securing them together with an M3x12
BHCS and M3 hex nut.

Z TENSIONER PULLEY
Take the F623 bearing stack and place them
between the idler securing them using an
M3x20 BHCS. Note the direction the screw
is going, it will always go from the Inside of
the printer to the outside

Z IDLERS; MICRON; M3x20 BHCS

Z IDLER MOUNTING
mounting the Z idlers on the top of the
frame along the side extrusion.

BED PREP | MICRON

BED HEATER
The bed uses a silicone heater this can be powered by either AC mains voltage or DC 24v. Make sure if you use an AC mains voltage bed to add a ground wire as well as a thermal fuse in line on the L line of the mains wiring. .

ALIGNMENT PINS
The bed should have 2 m3 tapped holes in the back of it. These are for 2 M3X12 BHCS. These act as alignment pins for the spring steel flex plate print surface. These screws come up from the bottom of the bed.

M3x12 BHCS

BED SCREWS
Depending on the thickness of the bed
and height of the m4 thumbnuts the bed
mounting screws can range from M3x16
to M3x20 just make sure you have the
bed snugged down properly

WAIT..WHERE IS THE REST OF THE
FRAME?
The bed install guide is purposefully not
showing the rest of the printer frame so
the bed installation can be shown much
easier.

GANTRY ASSEMBLY; MICRON

Y AXIS LINEAR RAILS
There are 2 linear rails on the Y-axis mounted to
the C extrusions and they both need to be
exactly centered.

X RAIL; MICRON; M3x8 BHCS

X Axis Linear Rail
As with the Y linear rail , the X
rail also needs to be perfectly
centered on the D extrusion.

Screws too long?
Some kits have shown that m3x8s
may be too long, if that is the case
swap these for m3x6.

Z JOINTS | MICRON

Z JOINTS | MICRON

Z JOINTS | MICRON

Z JOINTS | MICRON

Z JOINTS | MICRON

Z JOINTS | MICRON

Z JOINTS | MICRON

Z JOINTS | MICRON

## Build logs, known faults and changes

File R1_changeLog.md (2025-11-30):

## Changes From R0 
### Gantry 
  * AB Drives
    * supports pinned bearings/pulleys or screws (pins are 25mm)
    * option for adding a top bearing support for stepper motor shafts (uses F695 bearings)
    * Fixed all belt path issues with the gantry
    * integrated Y endstop/sensorless endstop 
  * Gave every piece a low poly / stealthy look to them
  * Z Joints
    * updated KGLM z joints so they are less prone to cracking
    * Added Rigid Z joints
  * XY Joints
    * Stock build now uses Toothed idlers
    * supports pinned bearings/pulleys or screws (pins are 25mm)
    * option to use Live Idlers
  * Front Idlers
    * Implemented the BFI idlers for the AB belts
    * Modified the BFI idlers from clees repo to fix the belt path for the R1 gantry
    * supports pinned bearings or screws (pins are 14mm)
  * Rear Gantry Changes 
    * Swapped rear extrusion and Z chain to give more room for toolhead board wiring/umbilical
    * Removed support for the printed Z chain
    * Z-Chain guide now has chamber thermistor mount
    * New klicky probe dock that keys into the B drive
  * X Carriage
    * No changes to the X carriage
    * New probe mounts, now supports the following probes also includes a printed sensorless endstop bumper for X 
      * Beacon/Cartographer
      * Klicky
      * KlickyPCB
      * BIQU Microprobe
  * Toolhead 
    * [Anthead](https://github.com/PrintersForAnts/AntHead) is now the stock toolhead

### Z axis
  * Z Drives
    * Z drives now use 152mm belt loops to keep the entire assembly really compact
    * screw driven closed loop belt tensioning
    * supports nema14 / 17 (up to 52 mm long motors)
    * Option for G2Z Z drives now supported with matching skirts
  * Z Idlers
    * BZI idlers for the Z belts
    * Modified BZI to support both toothed idlers and bearing stacks (there are different parts named accordingly)
    * Option for live Idlers Z idlers
    * supports pinned bearings or screws (pins are 18mm)

### Panels/Door/Skirts
  * Door
    * New door hinge/ latch system that no longer needs the magnet latch on the inside of the printer
    * Door now needs 3mm foam to help seal the enclosure better
  * Panel clips
    * 2 new panel clip options 
    * Toolless twist lock panel clip
    * screwed on panel clips
    * There is a parametric panel clip [CAD file](https://github.com/PrintersForAnts/Micron/blob/main/CAD/SubAssemblies.zip) so you can get custom sized for your build if needed (stock uses 3mm foam and 3mm panels)
    * reverse bowden tube entry now has multiple versions for different types of collets
    * ptfe guide attaches via twist lock setup similar to panel clips
    * Spool holder is now 2 pieces so it can be stored flat when not needed
  * Bottom Panels screw holes have been moved (Bottom panel is not required in the build)
  * Z Belt Panel covers have been updated with a new insert to cover the hole to help keep out debris
  * Skirts
    * All new Skirts to match the new aesthetic
    * Rear Skirts
      * Rear skirt now includes 2 keystone slots
      * Option for filtered power Inlets
    * Front Skirt
      * Headless option now has all the hexes in the grid are centered correctly (previous version was not)
      * Added [BTT TFT35](https://s.click.aliexpress.com/e/_on454Nj) display mount
      * Added [Waveshare 4.3](https://www.waveshare.com/4.3inch-dsi-lcd.htm) and [BTT43](https://s.click.aliexpress.com/e/_oCLFmxB) mount (same mount for both displays)
    
### Accessories
  * Filter
    * New carbon filter added to mount under the bed
    * Uses a single 5015 fan for the filter
  * Bed heater / air circulation fans
    *   Dual 5015 bed fans
    *   Printed part replaces the stock Z belt covers on the front of the printer
  * Handles have been updated to be easier to mount , no longer need to be removed to remove top panel

## 
  
## Commit Change log ##

### 06-15-2025
* Added dedicated Pinned version for the front idler carrier 

### 04-15-2025
* added dual 5015 bed fan option
* updated filter cartridge and catridge lid to match the new bed fans
* updated CAD assembly to RC3 with all the latest changes

### 03-03-2025
* fixed [#148](https://github.com/PrintersForAnts/Micron/issues/148)
* fixed [#149](https://github.com/PrintersForAnts/Micron/issues/149)

### 02-05-2025
* added missing parts to the CAD assembly caused by a bad export 

### 01-28-2025
* fixed issue with bearings rubbing on the A drive
* closed up the Z belt holes in the AB drives and front idlers and made them more symmetrical

### 01-20-2025
* fixed issues #143 , #141, #138 , #137
* Updated CAD to RC1 status
* uploaded WIP manual with updated preloaded nut callouts 

### 10-17-2024
* Added G2Z Cad and organized all the STLS (Z drives and skirts) G2Z uses same foot mounts from R1Z and skirt accent pieces 
* fixed Pinned XY joints hole sizes to now all be 3.2mm 
* Updated latest assembly to include [Anthead](https://github.com/PrintersForAnts/AntHead)

### 9-20-2024
* increased tension travel on the front idlers by 5mm (from 3mm to 8mm) , minor changes to the front cover of the idler as well

### 9-18-2024
* fixed incorrect counterbore bridging on the rear bowden entry files (thanks to user named Yell for finding that)

### 9-12-2024
* added CNC gantry top bearing mount
* Updated all the umbilical mounts to accomodate the new top bearing mount, as it was interfearing
* removed the YC8 version of the umbilical
* updated cad assembly to v59 

### 9-10-2024
* Added new top bearing support for a double shear bearing on the AB motors 

### 9-5-2024
* cleaned up main cad assembly 
* posted link to fusion source assembly file to be downloaded
* adjusted gantry files to no longer need built in printed shim, now there are shims on both sides of every bearing stack 

### 9-3-2024
* added missing filter files 
* fixed naming issues on certain files 

### 9-2-2024
* added new under bed carbon filter
* started on CAD assembly clean up 
* renamed various files 

### 8-22-2024 
* cleaned up files

### 8-11-2024
* updated the Hula foot mounts to the latest version that works with the bottom panel
* added new TFT35 display front skirt 
* updated latest cad assembly v55
* removed old cad files no longer needed (moved hula cad files into main assembly)

### 8-2-2024
* organized panel clip files
* updated latest cad assembly v54
* added dual color rear bowden entry option

### 8-1-2024
* Updated Z drives for better printability to match new skirt accent pieces
* Added under bed filter from KyleGB to the main repo (still need STLs)

### 7-27-2024
* fixed waveshare accent pieces
* updated latest cad assembly v52
* updated skirts with new accent pieces as well as bottom panel mounting provisions

### 7-25-2024
* Updated z belt cover accent cover to fit better
* added twist lock panel clips for 3mm foam and panels
* fixed printing orientation for rail stops and umbilical mounts

### 7-23-2024
* Updated R1 Skirts to now include accent strips along the bottom as well as allow for a bottom panel to fit
* Updated skirts to they are all the same height , some had about ~1mm difference between them 
* Updated the waveshare mount to now us m2 self tapping screws instead of filament to keep bezel on 
* Updated Z drive foot mount to accommodate  bottom panel 

### 7-23-2024
* Update Beacon mount to work with older Rev D beacon probes 
* Added a new rear bowden entry set, supporting m10 collet, ECAS collet, or No collet 
* Added R1 style stock panel clips (tool less panel clips are coming soon as an option as well)
* Added fixed Z belt covers to better fit with the R1 Z belt location
* Organized the panel file directory 

### 7-15-2024
* Added Beacon probe mount

### 7-08-2024
* Added 120x120 build R1 Cad assembly
* Added rear skirts for 120x120 builds 
* Organized files into 120 and 180 specific folders 

### 7-05-2024
* added rear power inlet skirts
* updated printed rail stops to match the style of R1 update (low poly look)
* added keystone blank model to fill the keystone slots on the rear skirt if not used 

### 7-02-2024
* updated Z drive tensioner body to use longer m3x25 instead of m3x20
* added optional Hula feet adapters for R1 and G2Z
* updated latest cad assembly

### 6-18-2024
* uploaded side skirts and 4.3 waveshare display front skirt

### 6-2-2024
* changed hex pattern on Z drives to make them easier to print 

### 5-21-2024
* adjust the location of the Z gantry belts pulley to fit in the front idlers better ([#124](https://github.com/PrintersForAnts/Micron/issues/124))

### 5-14-2024
* fixed z drive issue with inconsistencies with both A and B z drives ([#120](https://github.com/PrintersForAnts/Micron/issues/120))
* updated z tensioner bearing overhang to be easier to print ([#122](https://github.com/PrintersForAnts/Micron/issues/122))

### 5-7-2024
* Added ziptie spot on to klicky dock

### 5-6-2024
 * Updated Z drives to fit powge and formbot metal 64T pulleys ([#115](https://github.com/PrintersForAnts/Micron/issues/115))
 * Updated Z idlers to fit toothed pulleys with a flange of 13mm OD ([#116](https://github.com/PrintersForAnts/Micron/issues/116))
 * raised klicky dock , it was hanging too low ([#117](https://github.com/PrintersForAnts/Micron/issues/117))
 * updated spool holder to now work with 3mm foam ([#118](https://github.com/PrintersForAnts/Micron/issues/118))

### 4-6-2024
 * added pushed rigid z joints
 * new z belt covers
 * new bowden tube holder
 * new removable spool holder (modified from LDOs)

### 4-5-2024
  *  Added Nema14 Z motor mounts

### 4-3-2024
  * New beta rev2 Z drives with the 152mm belt loops
  * Shrunk entire body by 5mm or so
  * rotated the Z drives 180deg, this makes it easier to retention the closed loop belts after they are assembled if needed (thanks [@Squirrel-brain](https://github.com/Squirrel-brain)) 

## BOM Changes (Subject to change)
Item  |Qty | Notes
 ----|----|----|
GT2-16-Toothed Idler | 6 | XY-Joints and Z idlers now use toothed idlers by default, bearing stacks will still work 
GT2-152mm closed loop belt | 4 | New Z drives use 152mm belt loops instead of the 188mm 
screws | IDK | i havent gone through and checked the changes for the hardware as of yet 
MGN9H | 1 | X rail is now going to be spec as an MGN9H rail instead of MGN9C to support boop natively 
Klicky_PCB | 1 | now offical support optional as standard klikcy is still supported 
BIQU_microprobe | 1 | also now an official supported mount for those that want to use it

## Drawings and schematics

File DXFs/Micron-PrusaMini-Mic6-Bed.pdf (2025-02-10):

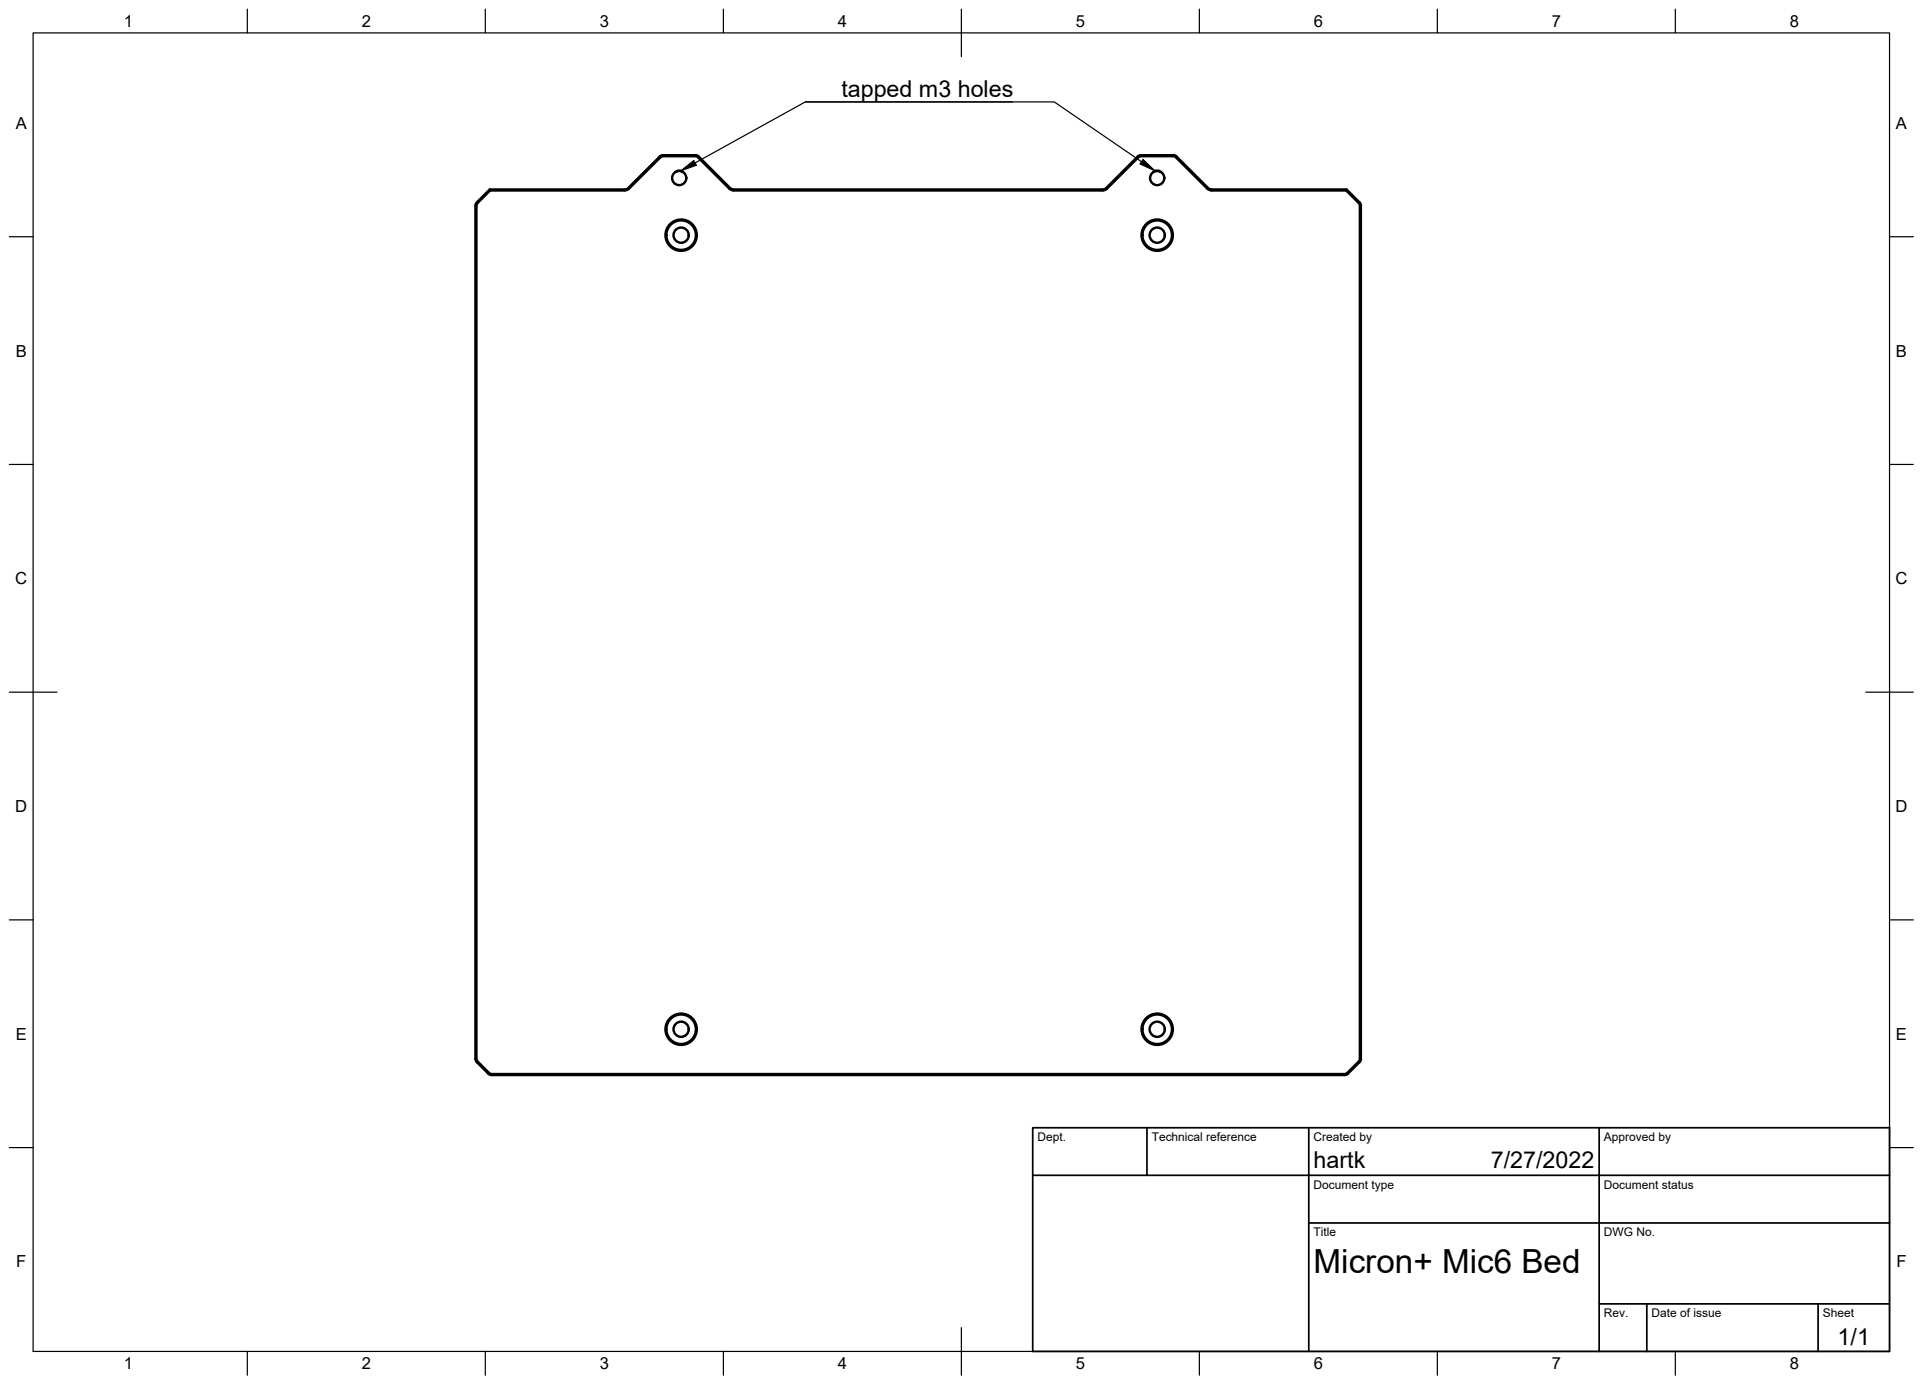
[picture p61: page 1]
Title; DWG No.; Rev.; Date of issue; Sheet; Micron+ Mic6 Bed; tapped m3 holes

Dept. | Technical reference | Created by hartk 7/27/2022 | Approved by

Document type | Document status

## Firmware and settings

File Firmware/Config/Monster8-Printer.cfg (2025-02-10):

# This file contains common pin mappings for MKS Monster8
# boards. To use this config, the firmware should be compiled for the
# stm32f407. When running "make menuconfig", select the 48KiB
# bootloader, and enable "USB for communication".

# The "make flash" command does not work on the MKS Monster8. Instead,
# after running "make", copy the generated "out/klipper.bin" file to a
# file named "mks_monster8.bin" on an SD card or Udisk and then restart the
# MKS Monster8 with that SD card or Udisk.

# See docs/Config_Reference.md for a description of parameters.

## Micron/Micron+ MKS Monster8 v1/v2 TMC2209 UART config

## *** THINGS TO CHANGE/CHECK: ***
## MCU paths                            [mcu] section
## Thermistor types                     [extruder] and [heater_bed] sections - See 'sensor types' list at end of file
## Z Endstop Switch location            [safe_z_home] section
## Homing end position                  [gcode_macro G32] section
## Z Endstop Switch  offset for Z0      [stepper_z] section
## Probe points                         [quad_gantry_level] section
## Min & Max gantry corner postions     [quad_gantry_level] section
## PID tune                             [extruder] and [heater_bed] sections
## Thermistor types                     [extruder] and [heater_bed] sections
## Probe pin                            [probe] section
## Fine tune E steps                    [extruder] section


#####################################################################
#   Important other files
#####################################################################

[include Klicky/klicky-probe.cfg]

[mcu]
##  Obtain definition by "ls -l /dev/serial/by-id/" then unplug to verify
##--------------------------------------------------------------------
serial: /dev/serial/by-id/{REPLACE WITH YOUR SERIAL}
restart_method: command
##--------------------------------------------------------------------

[printer]
kinematics: corexy
max_velocity: 300  
max_accel: 3000             #Max 4000
max_z_velocity: 15          #Max 15 for 12V TMC Drivers, can increase for 24V
max_z_accel: 350
square_corner_velocity: 5.0

#####################################################################
#   X/Y Stepper Settings
#####################################################################

##  B Stepper - Left
##  Connected to MOTOR_0
##  Endstop connected to DIAG_0
[stepper_x]
step_pin: PC14
dir_pin: !PC13
enable_pin: !PC15
rotation_distance: 32
microsteps: 32
full_steps_per_rotation:200
endstop_pin: PA14
position_min: 0
##--------------------------------------------------------------------

##  Uncomment below for Micron build
#position_endstop: 115
#position_max: 115

##  Uncomment for Micron+ build
#position_endstop: 180
#position_max: 180

##--------------------------------------------------------------------
homing_speed: 50   #Max 100
homing_retract_dist: 5
homing_positive_dir: true

[tmc2209 stepper_x]
uart_pin: PE6
interpolate: false
run_current: 0.6
sense_resistor: 0.110
stealthchop_threshold: 0

##  A Stepper - Right
##  Connected to MOTOR_1
##  Endstop connected to DIAG_1
[stepper_y]
step_pin: PE5
dir_pin: !PE4
enable_pin: !PC15
rotation_distance: 32
microsteps: 32
full_steps_per_rotation:200
endstop_pin: PA15
position_min: 0
##--------------------------------------------------------------------

##  Uncomment below for Micron build
#position_endstop: 123
#position_max: 123

##  Uncomment for Micron+ build
#position_endstop: 190
#position_max: 190

##--------------------------------------------------------------------
homing_speed: 50   #Max 100
homing_retract_dist: 5
homing_positive_dir: true

[tmc2209 stepper_y]
uart_pin: PE3
interpolate: false
run_current: 0.6
sense_resistor: 0.110
stealthchop_threshold: 0

#####################################################################
#   Z Stepper Settings
#####################################################################

## Z0 Stepper - Front Left
##  Connected to MOTOR_2
##  Endstop connected to DIAG_2
[stepper_z]
step_pin: PE1
dir_pin: !PE0
enable_pin: !PE2
rotation_distance: 32
gear_ratio: 64:16
microsteps: 32
endstop_pin: PB13
#endstop_pin: probe:z_virtual_endstop
##  Z-position of nozzle (in mm) to z-endstop trigger point relative to print surface (Z0)
##  (+) value = endstop above Z0, (-) value = endstop below
##  Increasing position_endstop brings nozzle closer to the bed
##  After you run Z_ENDSTOP_CALIBRATE, position_endstop will be stored at the very end of your config
position_endstop: -0.5
##--------------------------------------------------------------------

##  Uncomment below for Micron build
#position_max: 110

##  Uncomment below for Micron+ build
#position_max: 165

##--------------------------------------------------------------------
position_min: -5
homing_speed: 8
second_homing_speed: 3
homing_retract_dist: 3

[tmc2209 stepper_z]
uart_pin: PB7
interpolate: false
run_current: 0.6
sense_resistor: 0.110
stealthchop_threshold: 0

##  Z1 Stepper - Rear Left
##  Connected to MOTOR_3
[stepper_z1]
step_pin: PB5
dir_pin: PB4
enable_pin: !PB6
rotation_distance: 32
gear_ratio: 64:16
microsteps: 32

[tmc2209 stepper_z1]
uart_pin: PB3
interpolate: false
run_current: 0.6
sense_resistor: 0.110
stealthchop_threshold: 0

##  Z2 Stepper - Rear Right
##  Connected to MOTOR_4
[stepper_z2]
step_pin: PD6
dir_pin: !PD5
enable_pin: !PD7
rotation_distance: 32
gear_ratio: 64:16
microsteps: 32

[tmc2209 stepper_z2]
uart_pin: PD4
interpolate: false
run_current: 0.6
sense_resistor: 0.110
stealthchop_threshold: 0

##  Z3 Stepper - Front Right
##  Connected to MOTOR_5
[stepper_z3]
step_pin: PD2
dir_pin: PD1
enable_pin: !PD3
rotation_distance: 32
gear_ratio: 64:16
microsteps: 32

[tmc2209 stepper_z3]
uart_pin: PD0
interpolate: false
run_current: 0.6
sense_resistor: 0.110
stealthchop_threshold: 0

#####################################################################
#   Extruder
#####################################################################

##  Connected to MOTOR_6
##  Heater - HE0
##  Thermistor - T0
[extruder]
step_pin: PC7
dir_pin: PC6
enable_pin: !PC8
##  Update value below when you perform extruder calibration
##  If you ask for 100mm of filament, but in reality it is 98mm:
##  rotation_distance = <previous_rotation_distance> * <actual_extrude_distance> / 100
##  22.6789511 is a good starting point
rotation_distance: 22.6789511   #Bondtech 5mm Drive Gears
gear_ratio: 50:10              #BMG Gear Ratio
microsteps: 32
full_steps_per_rotation: 200    #200 for 1.8 degree, 400 for 0.9 degree
nozzle_diameter: 0.400
filament_diameter: 1.75
heater_pin: PB0
## Check what thermistor type you have. See https://www.klipper3d.org/Config_Reference.html#common-thermistors for common thermistor types.
## Use "Generic 3950" for NTC 100k 3950 thermistors
#sensor_type:
sensor_pin: PC1
min_temp: 10
max_temp: 270
max_power: 1.0
min_extrude_temp: 170
control = pid
pid_kp = 26.213
pid_ki = 1.304
pid_kd = 131.721
##  Try to keep pressure_advance below 1.0
#pressure_advance: 0.05
##  Default is 0.040, leave stock
#pressure_advance_smooth_time: 0.040

##  E0 on MOTOR6
[tmc2209 extruder]
uart_pin: PD15
interpolate: false
run_current: 0.3
sense_resistor: 0.110
stealthchop_threshold: 0

#####################################################################
#   Bed Heater
#####################################################################

[heater_bed]
##  Heater Pin - BED_OUT - PB10
##  Thermistor - TB - PC0
heater_pin: PB10
##  Validate the following thermistor type to make sure it is correct
##  See https://www.klipper3d.org/Config_Reference.html#common-thermistors for additional options
#sensor_type: Generic 3950
max_power: 0.6
sensor_pin: PC0
min_temp: 0
max_temp: 120
control: pid
pid_kp: 58.437
pid_ki: 2.347
pid_kd: 363.769

#####################################################################
#   Probe
#####################################################################

[probe]
##  Klicky Probe - Since this is just an endstop switch its wired up to one of the endstop ports
pin: PB13
x_offset: 0
y_offset: 26.0
z_offset: 0
speed: 10.0
samples: 3
samples_result: median
sample_retract_dist: 3.0
samples_tolerance: 0.006
samples_tolerance_retries: 3

#####################################################################
#   Fan Control
#####################################################################

[fan]
##  Print Cooling Fan - FAN0 - MAKE SURE TO SET THE VOLTAGE JUMPER TO 5V , MOST 3007 FANS ARE 5V
pin: PA2
kick_start_time: 0.5
##  Depending on your fan, you may need to increase this value
##  if your fan will not start. Can change cycle_time (increase)
##  if your fan is not able to slow down effectively
off_below: 0.10

[heater_fan hotend_fan]
##  Hotend Fan - FAN1
pin: PA1
max_power: 1.0
kick_start_time: 0.5
heater: extruder
heater_temp: 50.0
##  If you are experiencing back flow, you can reduce fan_speed
#fan_speed: 1.0
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

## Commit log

2025-02-10 Clean up, match with voron design repo structure
    [180_bottom_panel.dxf, BLACK_DeckPanel_x1.dxf, BLACK_RearPanel_x1.dxf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]
2025-02-10 Move Firmware/Slicer/BedModel to Slicer_Profiles/BedModel
    [micron-bed-model-simple-120.stl, micron-bed-model-simple-160.stl, micron-bed-model-simple-180.stl]
2025-02-10 Add Monster8-Printer.cfg
    [Monster8-Printer.cfg]
2026-01-02 Adds low profile DIN brackets
    [FLY_D8_din_bracket_low_profile_x1.stl, FLY_D8_fan_duct_x1.stl, Heat Insert Helper for 6mm hole.stl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]
2026-01-02 Add thicker 1515 din rail mount
    Better strength for shorter din rails
    as 280/210mm flush length may struggle to fit in
    this allows din rails to be 5-10mm shorter than extrusion
    [1515_Din_rail_mount_5mm_x4.stl, 1515_Din_rail_mount_8mm_x4.stl]
